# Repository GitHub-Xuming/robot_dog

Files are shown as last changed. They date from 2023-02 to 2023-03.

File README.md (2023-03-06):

# 开源四足机器狗
## 开源资料说明
* 硬件资料

Hardware/Model目录包含所有零件模型文件
* 软件资料

Software/Linux目录为上位机控制软件  
Software/STM32目录为单片机程序
## B站视频地址  
https://www.bilibili.com/video/BV1pX4y1D7ny/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
## 机械结构设计

    1.整机由12自由度四足机器狗以及一台6轴机械臂组成，四足机器人腿部采用了五连杆机构，之所以采用这样的结构，源于五连杆机构具有更大的承载  
    能力以及更好的刚性，但是也有它的缺点，运动范围相对串联腿小，不能做太大幅度动作，这个版本先使用并联腿，后面可以优化为串联结构！        
    2.五连杆两摆动臂采用浮动设计，中间加入减震弹簧，能减少对电机的冲击  
    3.腿部外伸自由度使用同步轮减速，减速比2.4，可以加大转矩以及减小电机间隙对输出的影响
    4.机身主要由两条碳纤维方管作为骨架支撑整个身体，其他运动部件以它为基准
    5.机械臂连杆使用碳纤维圆管连接
    6.机械臂末端安装机械爪，夹爪有弹簧缓冲结构  
## 关于舵机  

    1.机器狗使用12个mg958舵机，在对比多款舵机后，这个舵机是我认为性价比最高的，6.6V供电实测堵转扭矩能到18kg/cm,堵转电流5A，  
    响应速度也很OK,具体没测。6.6V供电电压由10个5A的降压模块而来，因舵机功率较大，所以受力较大的舵机都单独配一个降压模块，  
    这样一来整机的承载能力还是很可观的，具体可观看此视频：https://www.bilibili.com/video/BV1Lp4y1C75n/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
    2.机械臂电机使用总线舵机，某宝上买来的优必选舵机，10块钱左右一个，结合网友给出的研究资料（百度搜索白菜价舵机），成功驱动。  
    末端三个自由度使用的也是优必选的较小的一款，波特率1M，协议一致。整体来说，机械臂成本还是很低的
    
## 关于电路  
    开源资料未提供电路图，使用到的电路都非常简单  
    1.PWM舵机使用一组光耦隔离电路，总线舵机以及其他外设直接接单片机  
    2.FSR力传感器串联一个分压电阻直接接单片机  
    3.电源用继电器和二极管做了防反接保护，单片机和外设供电使用7805降压芯片  
 
## 关于板级通信
    控制器由BeagleBoneBlack开发板作为上位机，所有控制算法在上面完成，型号为STM32f407的单片机作为下位机，运行FreeRTOS操作系统
    负责外设数据采集和将上位机指令实时写到外设。  
    
    上位机与单片机通信使用的是全双工串口，以1M波特率运行，上位机实现了阻塞队列可多线程发起对单片机的传感器数据请求，单片机收到  
    请求后，立即采集数据并回复，同时上位机对当前数据进行计算，再下发控制数据到单片机... 整个过程看起开很繁琐，但是具有很高的实  
    时性，通过示波器观察，从上位机下发请求开始，到上位机再次下发完成控制数据，一共花费1.7ms
    
## 关于控制算法  
    重点说下鸡头模式原理，主要使用坐标系变换思想做到的，使用正向运动学以机器狗当前姿态为基础，将坐标系变换到机械臂坐标系，求逆矩阵，  
    再做逆向运动学，大概是这样的一个思路。  
    
    机械臂末端搭载了imu和光流传感器，都是用来测量末端的位移量，尝试了使用imu二次积分惯导解算位移，做闭环鸡头控制，无奈imu漂移太大，  
    整体效果较差，最终还是使用的了开环鸡头模式
    
    机器狗每条腿三个自由度，逆运动学使用代数法求解，可以得到三个角度，需要注意的是，有多组解，需要根据实际结构选择其中的一个，  
    机器狗扭身体动作原理同机械臂控制。

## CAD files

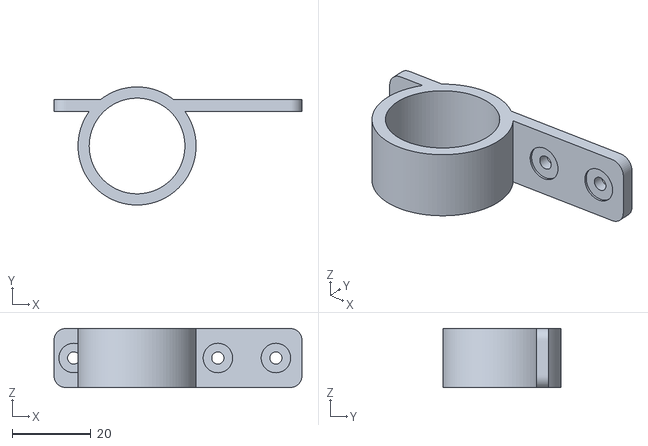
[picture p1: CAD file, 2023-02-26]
Hardtware/Model/同步轮支撑.stl
63.0 x 30.0 x 15.0

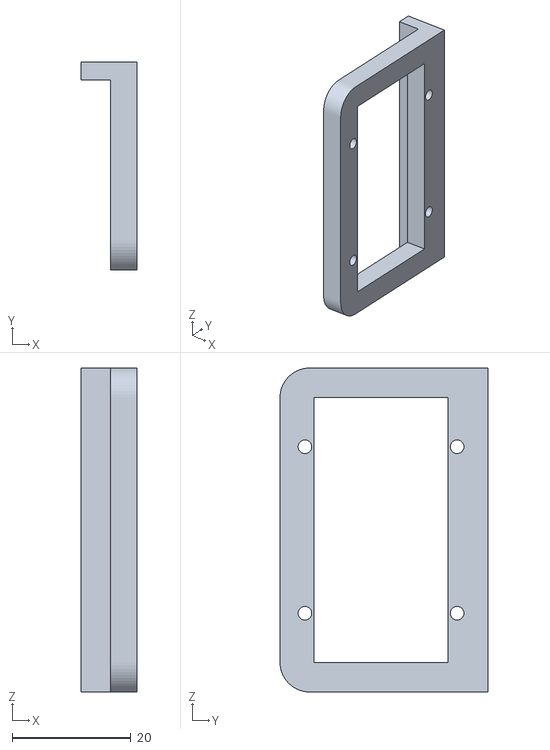
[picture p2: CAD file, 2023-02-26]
Hardtware/Model/机械臂旋转轴底座电机固定件2.stl
9.50 x 35.0 x 54.5

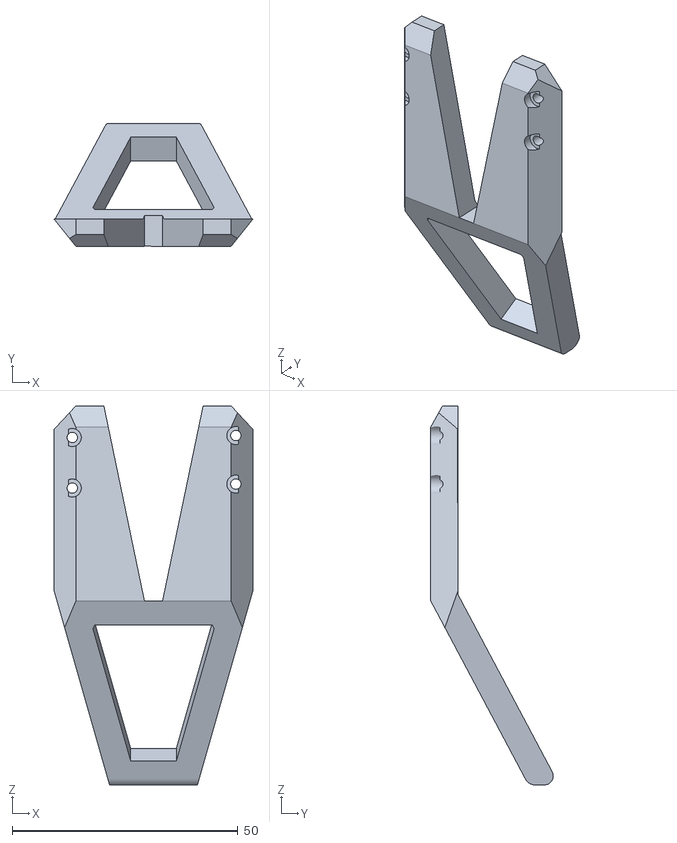
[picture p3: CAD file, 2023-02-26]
Hardtware/Model/机械爪上颌.stl
44.0 x 27.1 x 84.0

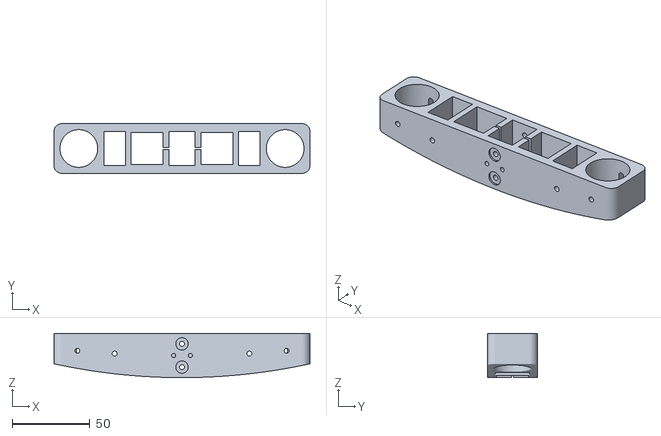
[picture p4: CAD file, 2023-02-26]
Hardtware/Model/机架1.stl
165.0 x 32.0 x 28.5

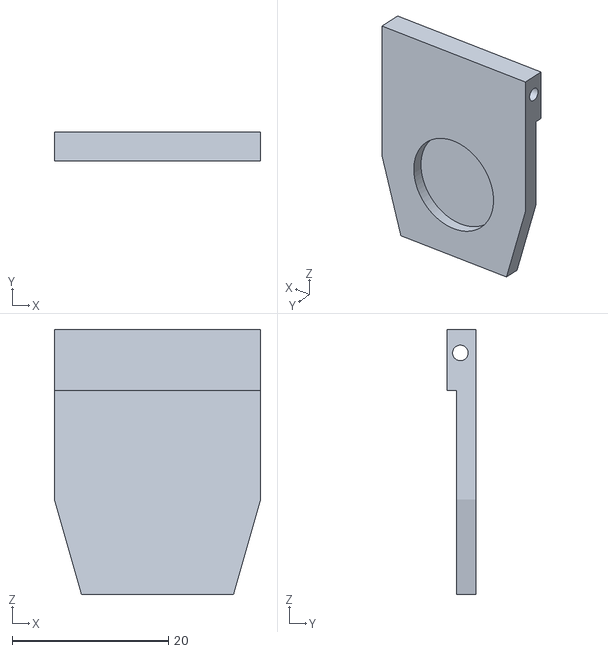
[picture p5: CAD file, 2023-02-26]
Hardtware/Model/机械爪FSR传感器座.stl
26.4 x 3.70 x 33.9

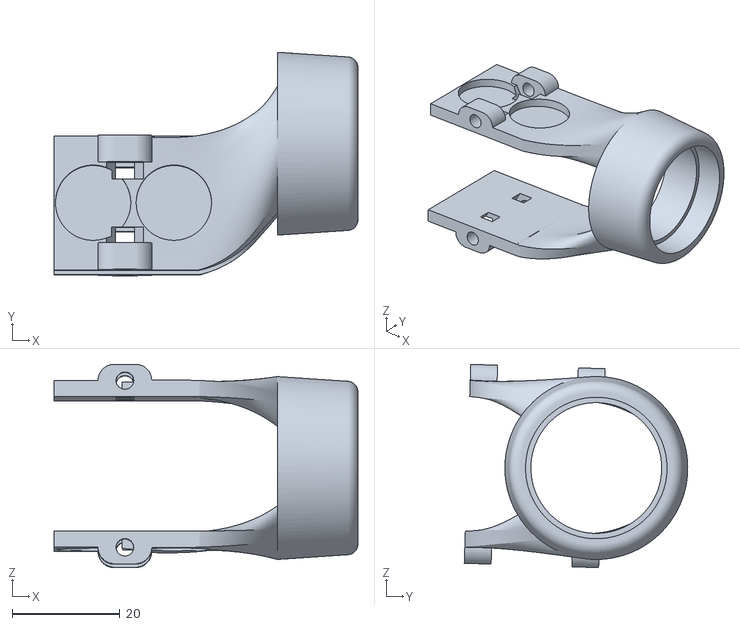
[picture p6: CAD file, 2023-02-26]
Hardtware/Model/腿部舵机输出支撑.stl
56.5 x 41.5 x 37.8

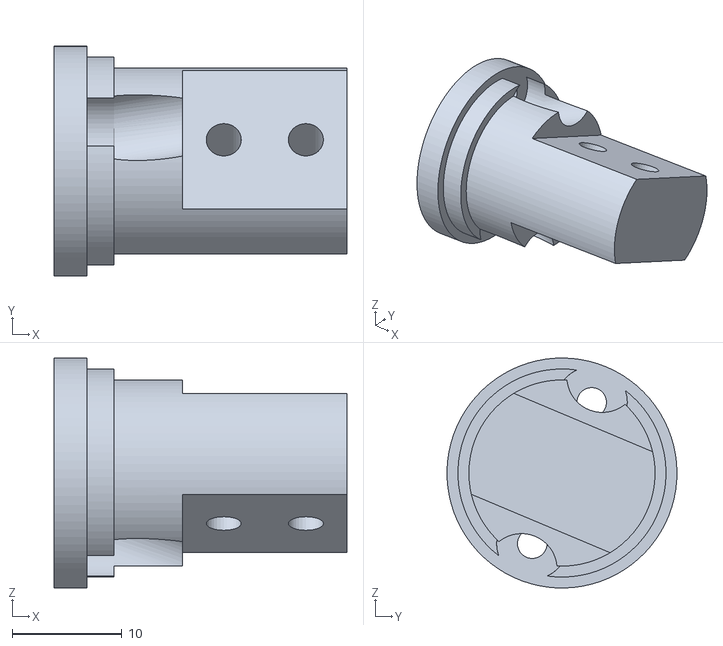
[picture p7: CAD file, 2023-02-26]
Hardtware/Model/腿部舵机法兰连接器.stl
26.8 x 21.0 x 21.0

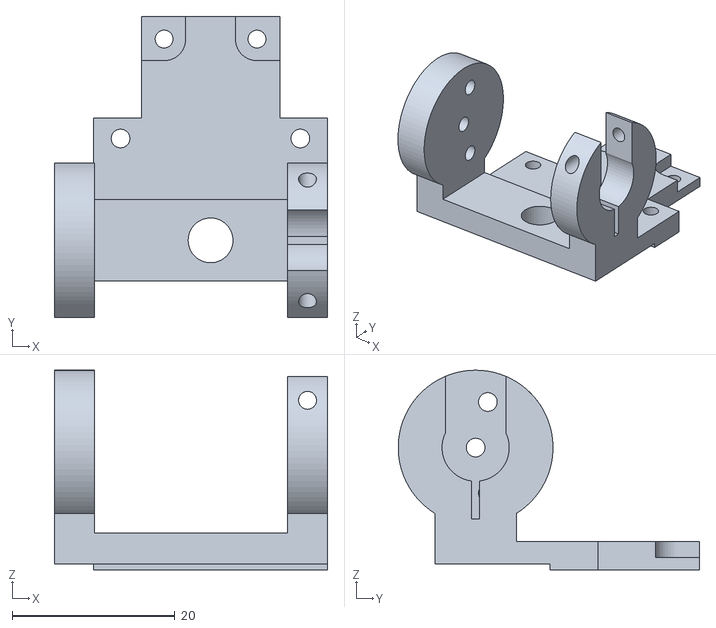
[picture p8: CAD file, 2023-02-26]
Hardtware/Model/机械臂五轴输出连接支架.stl
33.5 x 37.0 x 24.5

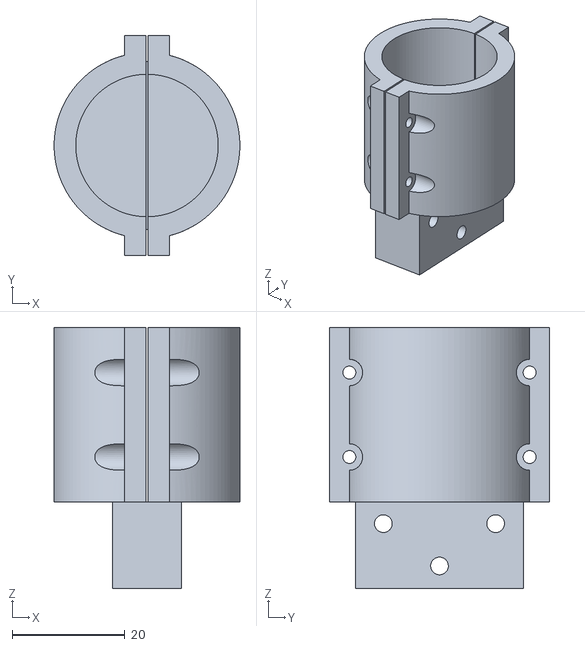
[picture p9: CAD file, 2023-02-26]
Hardtware/Model/机械臂二轴碳纤维连接件.stl
33.0 x 39.0 x 46.4

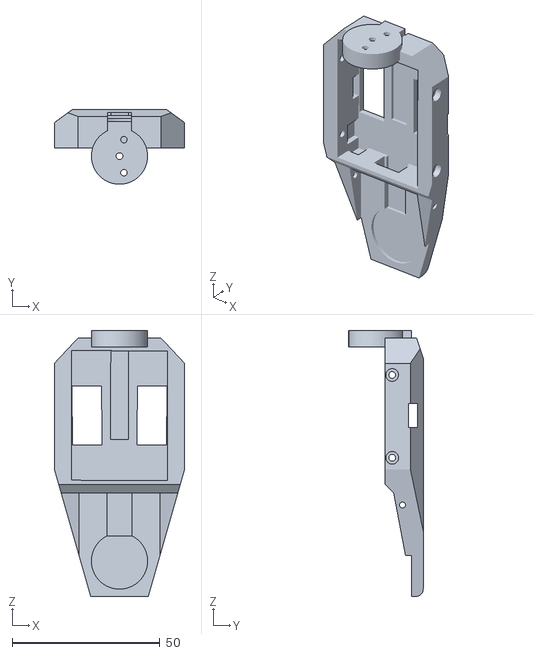
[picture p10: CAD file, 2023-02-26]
Hardtware/Model/机械爪底座.stl
44.0 x 25.2 x 89.9

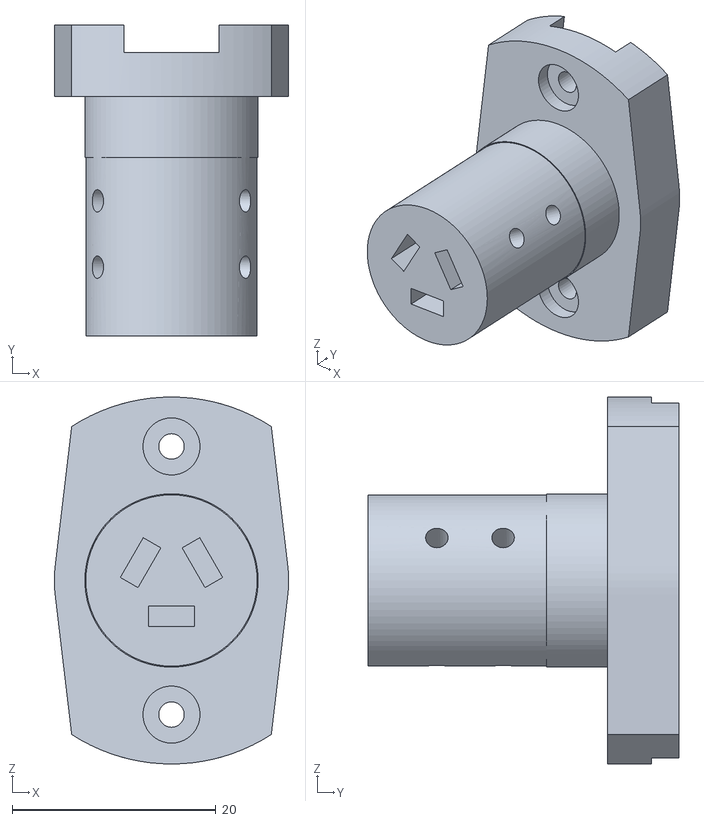
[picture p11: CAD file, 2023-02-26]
Hardtware/Model/机械臂底座电机输出轴.stl
23.0 x 30.5 x 36.0

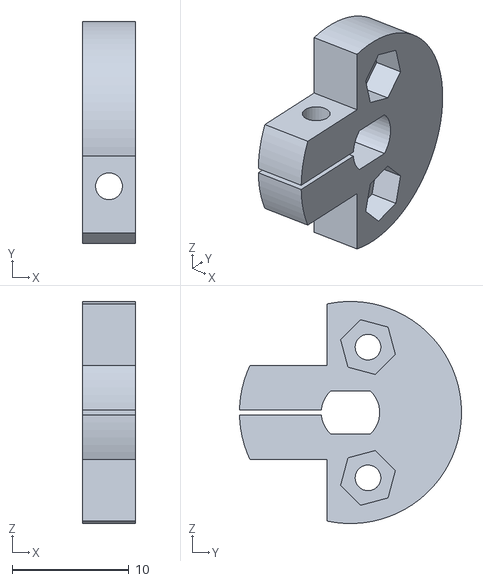
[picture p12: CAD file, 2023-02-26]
Hardtware/Model/机械臂五轴输出法兰盘.stl
4.50 x 19.0 x 19.0

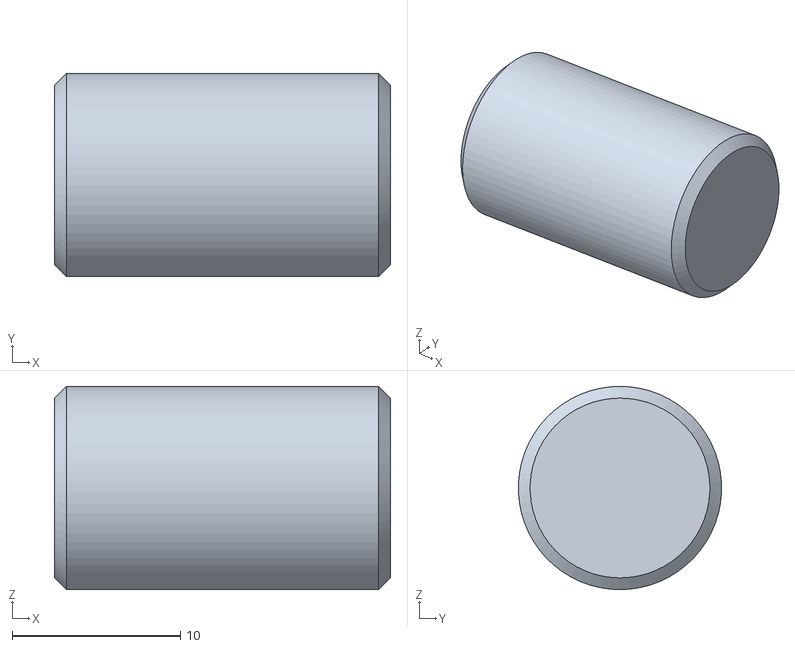
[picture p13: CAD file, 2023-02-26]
Hardtware/Model/腿部连杆轴.stl
20.0 x 12.1 x 12.1

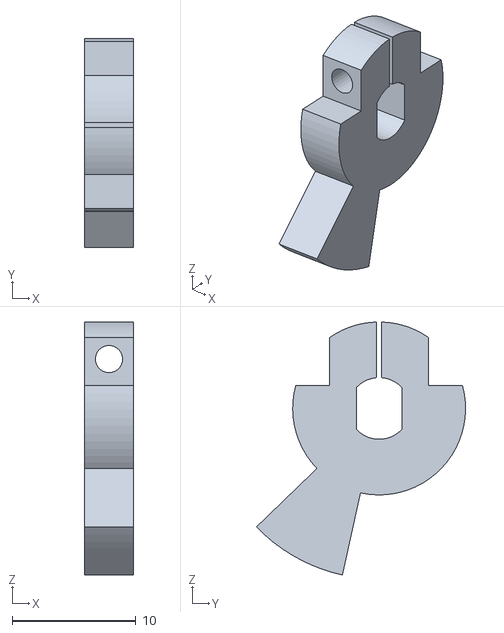
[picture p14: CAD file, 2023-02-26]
Hardtware/Model/机械爪电机输出轴法兰盘.stl
4.00 x 16.9 x 20.5

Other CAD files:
Hardtware/Model/机械臂四轴电机输出轴.stl
Hardtware/Model/机械爪电机输出轴.stl
Hardtware/Model/机械爪FSR传感器上盖.stl
Hardtware/Model/减震器弹簧座.stl
Hardtware/Model/减震器轴.stl
Hardtware/Model/同步轮减速电机座.stl
Hardtware/Model/同步轮大.stl
Hardtware/Model/同步轮小.stl
Hardtware/Model/同步轮边框大.stl
Hardtware/Model/同步轮连接器大.stl
Hardtware/Model/同步轮连接器小.stl
Hardtware/Model/机架2.stl
Hardtware/Model/机械爪上颌连接器1.stl
Hardtware/Model/机械爪上颌连接器2.stl
Hardtware/Model/机械爪减震机构2.stl
Hardtware/Model/机械臂三轴电机底座.stl
Hardtware/Model/机械臂三轴输出件1.stl
Hardtware/Model/机械臂三轴输出件2.stl
Hardtware/Model/机械臂二轴输出连接件.stl
Hardtware/Model/机械臂五轴碳纤维连接座.stl
Hardtware/Model/机械臂六轴电机固定支架.stl
Hardtware/Model/机械臂六轴输出法兰盘.stl
Hardtware/Model/机械臂四轴电机支架.stl
Hardtware/Model/机械臂四轴电机输出法兰盘.stl
Hardtware/Model/机械臂四轴输出支架.stl
Hardtware/Model/机械臂四轴输出碳纤维连接座.stl
Hardtware/Model/机械臂底座电机连接件1.stl
Hardtware/Model/机械臂底座电机连接件2.stl
Hardtware/Model/机械臂旋转轴底座.stl
Hardtware/Model/机械臂旋转轴底座电机固定件1.stl
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

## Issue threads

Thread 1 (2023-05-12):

The meaning of bodyPeakPoint

1874ruanshaodong, 2023-05-12:
Hi, what does bodyPeakPoint mean? Is it meaning that is the four vertices of the torso? Thanks.

GitHub-Xuming, 2023-05-13:
Yes, that’s correct. If we regard the four legs as four mechanical arms, then “bodyPeakPoint” is the origin position of each mechanical arm.

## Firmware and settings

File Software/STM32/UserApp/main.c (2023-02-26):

#include "robot_dog.h"
#include "robot_arm.h"
#include "timer.h"
#include "remote_ctrl.h"
#include "FreeRTOS.h"
#include "task.h"
#include "SEGGER_RTT.h"

int main()
{
	NVIC_PriorityGroupConfig(NVIC_PriorityGroup_4);	
	delay_init(168);
	SysTimerInit(1000 - 1, 84 - 1);
	SeggerInit();

	RemoteCtrlInit();
	ComHostInit();
	RobotArmInit();
	RobotDogInit();

	vTaskStartScheduler();
}

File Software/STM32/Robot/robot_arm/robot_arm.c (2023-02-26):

#include "robot_arm.h"
#include "math.h"
#include "usart3.h"
#include "uart4.h"
#include "delay.h"
#include "SEGGER_RTT.h"
#include "com_host.h"
#include "remote_ctrl.h"
#include "inertial_nav.h"
#include "FreeRTOS.h"
#include "task.h"
#include "semphr.h"

#define 	RobotArmCTRL_TASK_PRIO 			2  
#define 	RobotArmCTRL_STK_SIZE 			128 
#define 	ARM_ANGLE_ASK_TASK_PRIO 		2  
#define 	ARM_ANGLE_ASK_STK_SIZE 			128 
#define     ARM_CTRL_BAUD_RATE      		1000000 
#define     IMU_COM_BAUD_RATE      			921600 

TaskHandle_t Arm_Angle_Ask_Task_Handler; 
TaskHandle_t RobotArmCtrlTask_Handler;
void RobotArmAngleAskTask(void *p_arg); 
void RobotArmCtrlTask(void *p_arg); 
void RobotArmGPIO_Init();

uint8_t g_send_buff[10] = {FRAME_HEAD_1, FRAME_HEAD_2, 0x04, 0xD4, 0x00, 0x00, 0x00, 0x00};
uint8_t g_servo_kind = 0;
uint8_t g_id_convert_tb[7] = {1, 21, 3, 4, 5, 6, 7};

ACK_FRAM g_arm_res;
ServoInfo g_servo_info[7] = { 0 };
ArmAngle *g_arm_angle = NULL;
xSemaphoreHandle g_xArmAngleResSemaphore;
xSemaphoreHandle g_xRobotArmCtrlSemaphore;

/**
  * @brief  
  * @param  
  * @param 
  */
void RobotArmInit()
{
	Adc_Init();
	RobotArmGPIO_Init();
	Uart4Init(ARM_CTRL_BAUD_RATE); //机械臂
	//USART5_Init(IMU_COM_BAUD_RATE); //imu
	TIM1_CH1_Cap_Init(0xFFFF, 840 - 1); //光流传感器
	NavigationInit();
	/*servo 零点偏置初始化 原则：将舵机位置摆放到机械臂坐标系零点位置后，读取的角度值即为:offset*/
	g_servo_info[0].offset = 0;
	g_servo_info[1].offset = 0;
	g_servo_info[2].offset = 0;
	g_servo_info[3].offset = 0;
	g_servo_info[4].offset = 0;
	g_servo_info[5].offset = 120;
	g_servo_info[6].offset = 0;

	/*舵机id赋值，位置和读取标志清零*/
	for(int i = 0; i < 7; i++)
	{
		g_servo_info[i].id = g_id_convert_tb[i];
		g_servo_info[i].pos = 0;
		g_servo_info[i].read_flg = 0;
	}
	xTaskCreate((TaskFunction_t )RobotArmAngleAskTask,
		(const char* )"RobotArmAngleAskTask",
		(uint16_t )ARM_ANGLE_ASK_STK_SIZE,
		(void* )NULL,
		(UBaseType_t )ARM_ANGLE_ASK_TASK_PRIO,
		(TaskHandle_t* )&Arm_Angle_Ask_Task_Handler);

	xTaskCreate((TaskFunction_t )RobotArmCtrlTask,
		(const char* )"RobotArmCtrlTask",
		(uint16_t )RobotArmCTRL_STK_SIZE,
		(void* )NULL,
		(UBaseType_t )RobotArmCTRL_TASK_PRIO,
		(TaskHandle_t* )&RobotArmCtrlTask_Handler);
}

/**
  * @brief  
  * @param  
  * @param 
  */
void RobotArmGPIO_Init()
{ 
	GPIO_InitTypeDef  GPIO_InitStructure;
	RCC_AHB1PeriphClockCmd(RCC_AHB1Periph_GPIOD, ENABLE);

	GPIO_InitStructure.GPIO_Pin = GPIO_Pin_0 | GPIO_Pin_1;
	GPIO_InitStructure.GPIO_Mode = GPIO_Mode_OUT;
	GPIO_InitStructure.GPIO_OType = GPIO_OType_PP;
	GPIO_InitStructure.GPIO_Speed = GPIO_Speed_100MHz;
	GPIO_InitStructure.GPIO_PuPd = GPIO_PuPd_UP;
	GPIO_Init(GPIOD, &GPIO_InitStructure);

	GPIO_SetBits(GPIOD,GPIO_Pin_0 | GPIO_Pin_1);
	/*Arm角度请求信号量创建*/
	vSemaphoreCreateBinary(g_xArmAngleResSemaphore);
	if(g_xArmAngleResSemaphore != NULL)
	{
		xSemaphoreTake(g_xArmAngleResSemaphore, 0);
	}
	else
	{
		for(;;){}
	}
	/*Arm控制信号量创建*/
	vSemaphoreCreateBinary(g_xRobotArmCtrlSemaphore);
	if(g_xRobotArmCtrlSemaphore != NULL)
	{
		xSemaphoreTake(g_xRobotArmCtrlSemaphore, 0);
	}
	else
	{
		for(;;){}
	}
}

/**
  * @brief  
  * @param  
  * @param 
  */
void RobotArmAngleSemaphoreGive()
{
	portBASE_TYPE xHigherPriorityTaskWoken;
	xSemaphoreGiveFromISR(g_xArmAngleResSemaphore, &xHigherPriorityTaskWoken);
	if(xHigherPriorityTaskWoken)
	{
		portYIELD_FROM_ISR(xHigherPriorityTaskWoken);
	}
}

/**
  * @brief  
  * @param  
  * @param 
  */
void RobotArmCtrlSemaphoreGive()
{
	portBASE_TYPE xHigherPriorityTaskWoken;
	xSemaphoreGiveFromISR(g_xRobotArmCtrlSemaphore, &xHigherPriorityTaskWoken);
	if(xHigherPriorityTaskWoken)
	{
		portYIELD_FROM_ISR(xHigherPriorityTaskWoken);
	}
}

/**
  * @brief  
  * @param  
  * @param 
  */
void RobotArmAngleRes()
{
	g_arm_res.head = UART_DATA_HEAD;
	g_arm_res.function_code = TYPE_ARM_POS_RES; 
	g_arm_res.data_len = 14; 
	uint16_t tmp = 0;
	for(int i = 0; i < 7; i++)
	{
		tmp = g_servo_info[i].pos * ANGLE_CONVERT_RATE;
		g_arm_res.data[i * 2] = ((tmp >> 8) & 0x00ff);
		g_arm_res.data[i * 2 + 1] = (tmp & 0x00ff);
	}
	ComHostPacketToQueue(&g_arm_res, 0);
}

/**
  * @brief  
  * @param  
  * @param 
  */
void RobotArmAngleAskTask(void *p_arg)
{
	int flag_sum = 0;
	while(1)
	{
		if(xSemaphoreTake(g_xArmAngleResSemaphore, 100000) == pdTRUE)
		{
			USART_Cmd(UART4, ENABLE); 
			while(1)
			{
				RobotArmServoStartPosRead();  //正常情况下，发送函数执行完成，已经收到舵机回复了
				for(int i = 0; i < 7; i++)
				{
					flag_sum += g_servo_info[i].read_flg;
				}
				if(7 == flag_sum)
				{
					break;
				}
				flag_sum = 0;
				vTaskDelay(20);
			}
			USART_Cmd(UART4, DISABLE);  
			for(int i = 0; i < 7; i++)
			{
				g_servo_info[i].read_flg = 0;
			}
			RobotArmAngleRes();
		}
	}
}

/**
  * @brief  
  * @param  
  * @param 
  */
void RobotArmAngleCtrlValue(ArmAngle *angle)
{
	g_arm_angle = angle;
}

/**
  * @brief  
  * @param  
  * @param 
  */
void RobotArmCtrlTask(void *pvParameters)
{
	float delta_angle = 0.0;
	while(1)
	{
		if(xSemaphoreTake(g_xRobotArmCtrlSemaphore, 100000) == pdTRUE)
		{
			//send angle to servo
			RobotArmAllServoPosCtrl();
		}
	}
}

/**
  * @brief  
  * @param  
  * @param 
  */
void RobotArmAllServoPosCtrl()
{
	int ctrl_angle = 0;
	float delta_angle = 0.0;

	Uart4Init(115200);
	g_servo_kind = SERVO_BIG;
	for(int i = 0; i < 3; i++)
	{
		ctrl_angle = RobotArmServoAngleOptimizing(g_arm_angle->axis_angle[i]);
		delta_angle = ctrl_angle - g_servo_info[i].last_ctrl_angle; //突变计算
		if(ABS(delta_angle) < ARM_CTRL_SAFE_ANGLE)  //位置突变保护
		{
			if(i == 1)
			{
				RobotArmServoPosCtrl(22, RobotArmAxis2AngleConvert(ctrl_angle), 0, 0);
				vTaskDelay(2);  //必要延时，舵机回复数据较慢
			}
			RobotArmServoPosCtrl(g_id_convert_tb[i], ctrl_angle, 0, 0);
			vTaskDelay(2);
			g_servo_info[i].last_ctrl_angle = ctrl_angle;
		}
	}

	Uart4Init(1000000);
	g_servo_kind = SERVO_SMALL;
	for(int i = 3; i < 7; i++)
	{
		/*对控制的float角度进行优化处理*/
		ctrl_angle = RobotArmServoAngleOptimizing(g_arm_angle->axis_angle[i]);
		delta_angle = ctrl_angle - g_servo_info[i].last_ctrl_angle; //突变计算
		if(ABS(delta_angle) < ARM_CTRL_SAFE_ANGLE)  //位置突变保护
		{
			RobotArmServoPosCtrl(g_id_convert_tb[i], ctrl_angle, 0, 0);
			vTaskDelay(1);
			g_servo_info[i].last_ctrl_angle = ctrl_angle;
		}
	}
}

// float ConvertServo2Arm(ServoInfo *servo, float angle)
// {
// 	float out = 0;
// 	out = angle - servo->offset;
// 	return out < 0 ? (out + 360) : out;
// }

// float ConvertArm2Servo(ServoInfo *servo, float angle)
// {
// 	float out = 0;
// 	out = angle + servo->offset;
// 	return out > 360 ? (out - 360) : out;
// }

/**
  * @brief  
  * @param  
  * @param 
  */
void RobotArmCkeckAndSend()
{
	uint8_t check_sum = 0;

	for(int i = 2; i < 8; i++)
	{
		check_sum += g_send_buff[i];
	}
	g_send_buff[8] = check_sum;
	g_send_buff[9] = FRAME_TAIL;
	
	EN_T = 0;
	EN_R = 1;
	for(int i = 0; i < 10; i++)
	{
		Uart4SendByte(g_send_buff[i]);
	}
	if(g_servo_kind == SERVO_SMALL)
	{
		delay_us(30);  //min 6us
	}
	if(g_servo_kind == SERVO_BIG)
	{
		delay_us(70);  //min 6us
	}
	EN_T = 1;
	EN_R = 0;
}
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

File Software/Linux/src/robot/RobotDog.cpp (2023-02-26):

#include "RobotDog.h"
#include <math.h>
#include "my_debug.h"
#include "DataProgress.h"

using namespace std;

RobotDog::RobotDog()
{
	m_send_queue_ = std::make_shared<BlockQueue<std::vector<char>>>(10);

	/*leg编号初始化*/
	robot.legFR.leg_number = leg_1;
	robot.legBR.leg_number = leg_2;
	robot.legBL.leg_number = leg_3;
	robot.legFL.leg_number = leg_4;

	/*机器人body_move初始化*/
	robot.body.move_x = 0;
	robot.body.move_y = 0;
	robot.body.move_z = 0;

	/*机器人坐标系原点初始化*/
	robot.body.bodyCoorZeroPoint.x = 0;  
	robot.body.bodyCoorZeroPoint.y = 0;
	robot.body.bodyCoorZeroPoint.z = 0;

	/*机器人中心点偏移量初始化*/
	robot.body.body_centre_move_x = 0;
	robot.body.body_centre_move_y = 0;
	robot.body.body_centre_move_z = 0;

	/*四条腿顶点偏移*/
	robot.legFR.bodyPeakPoint.x = -(DOG_BODY_LENGTH/2.0 - robot.body.body_centre_move_x);
	robot.legFR.bodyPeakPoint.y = DOG_BODY_WIDE/2.0 - robot.body.body_centre_move_y;
	robot.legFR.bodyPeakPoint.z = 0;

	robot.legBR.bodyPeakPoint.x = DOG_BODY_LENGTH/2.0 + robot.body.body_centre_move_x;
	robot.legBR.bodyPeakPoint.y = DOG_BODY_WIDE/2.0 - robot.body.body_centre_move_y;
	robot.legBR.bodyPeakPoint.z = 0;

	robot.legBL.bodyPeakPoint.x = DOG_BODY_LENGTH/2.0 + robot.body.body_centre_move_x;
	robot.legBL.bodyPeakPoint.y = -(DOG_BODY_WIDE/2.0 + robot.body.body_centre_move_y);
	robot.legBL.bodyPeakPoint.z = 0;

	robot.legFL.bodyPeakPoint.x = -(DOG_BODY_LENGTH/2.0 - robot.body.body_centre_move_x);
	robot.legFL.bodyPeakPoint.y = -(DOG_BODY_WIDE/2.0 + robot.body.body_centre_move_y);
	robot.legFL.bodyPeakPoint.z = 0;

	m_send_data_.resize(24);
	m_thread_run_ = true;
	RobotDogRun();
}

RobotDog::~RobotDog()
{
	m_thread_run_ = false;
}

void RobotDog::RobotDogPoseFeedback(Pose &pose)
{
	m_robot_pose_.x = robot.body.moveVal.move_axis_x;
	m_robot_pose_.y = robot.body.moveVal.move_axis_y;
	m_robot_pose_.z = robot.body.moveVal.move_axis_z;
	m_robot_pose_.roll = robot.body.rotateVal.rot_axis_x;
	m_robot_pose_.pitch = robot.body.rotateVal.rot_axis_y;
	m_robot_pose_.yaw = robot.body.rotateVal.rot_axis_z;
	pose = m_robot_pose_;
}

void RobotDog::RobotDogCtrl(Pose posture, FootCoord foot_pos, std::vector<uint8_t> &out)
{
	robot.body.moveVal.move_axis_x = posture.x;
	robot.body.moveVal.move_axis_y = posture.y;
	robot.body.moveVal.move_axis_z = posture.z;
	robot.body.rotateVal.rot_axis_x = posture.roll;
	robot.body.rotateVal.rot_axis_y = posture.pitch;
	robot.body.rotateVal.rot_axis_z = posture.yaw;

	robot.legFR.world_coor_point.x = foot_pos.foot_FR.x;
	robot.legFR.world_coor_point.y = foot_pos.foot_FR.y;
	robot.legFR.world_coor_point.z = foot_pos.foot_FR.z;

	robot.legBR.world_coor_point.x = foot_pos.foot_BR.x;
	robot.legBR.world_coor_point.y = foot_pos.foot_BR.y;
	robot.legBR.world_coor_point.z = foot_pos.foot_BR.z;

	robot.legBL.world_coor_point.x = foot_pos.foot_BL.x;
	robot.legBL.world_coor_point.y = foot_pos.foot_BL.y;
	robot.legBL.world_coor_point.z = foot_pos.foot_BL.z;

	robot.legFL.world_coor_point.x = foot_pos.foot_FL.x;
	robot.legFL.world_coor_point.y = foot_pos.foot_FL.y;
	robot.legFL.world_coor_point.z = foot_pos.foot_FL.z;

	RobotDogProcessFlow();
	/*pos and en ctrl*/
	ServoAngleConstruct();
	out = m_send_data_;
}

void RobotDog::EN_Ctrl(bool en)
{
	RobotDogServoEnCtrl(en);
}

void RobotDog::RobotDogServoEnCtrl(bool ctrl)
{
	m_robot_enable_ = ctrl;
}

void RobotDog::RobotDogProcessFlow()
{
	/*控制body姿态，三个平移和旋转*/
	RobotDogRotMove(robot.body.rotateVal,robot.body.moveVal);

	/*正向运动学到各个关节，将世界坐标系描述的点转换到局部坐标系描述*/ 
	RobotDogInvForward(&robot.legFR);
	RobotDogInvForward(&robot.legBR);
	RobotDogInvForward(&robot.legBL);
	RobotDogInvForward(&robot.legFL);

	/*逆解，得到原始角度值*/
	LegInverseResolving(&robot.legFR);
	LegInverseResolving(&robot.legBR);
	LegInverseResolving(&robot.legBL);
	LegInverseResolving(&robot.legFL);

	/*得到五连杆机构的值*/
	GetFiveLinkAngle(&robot.legFR);
	GetFiveLinkAngle(&robot.legBR);
	GetFiveLinkAngle(&robot.legBL);
	GetFiveLinkAngle(&robot.legFL);

	/*转换到电机的角度值*/
	GetFiveLinkToMotor(&robot.legFR);
	GetFiveLinkToMotor(&robot.legBR);
	GetFiveLinkToMotor(&robot.legBL);
	GetFiveLinkToMotor(&robot.legFL);
}

void RobotDog::RobotDogRun()
{
    m_robot_thread_ = std::thread([this]
    {
        while(m_thread_run_) 
		{
			//TODO:
			std::this_thread::sleep_for(std::chrono::milliseconds(1000));    
		}
    });
}

void RobotDog::RobotDogRotMove(BodyRot rotateVal,BodyMove moveVal)
{
	float move_body[4][4] = { { 1,0,0,0 },{ 0,1,0,0 },{ 0,0,1,0 },{ 0,0,0,1 } };
	float ret_body_x[4][4] = { { 1,0,0,0 },{ 0,1,0,0 },{ 0,0,1,0 },{ 0,0,0,1 } };
	float ret_body_y[4][4] = { { 1,0,0,0 },{ 0,1,0,0 },{ 0,0,1,0 },{ 0,0,0,1 } };
	float ret_body_z[4][4] = { { 1,0,0,0 },{ 0,1,0,0 },{ 0,0,1,0 },{ 0,0,0,1 } };
	float mid_matrix_1[4][4] = { { 1,0,0,0 },{ 0,1,0,0 },{ 0,0,1,0 },{ 0,0,0,1 } };
	float mid_matrix_2[4][4] = { { 1,0,0,0 },{ 0,1,0,0 },{ 0,0,1,0 },{ 0,0,0,1 } };

	/*矩阵初始化*/
	move_body[0][3] = moveVal.move_axis_x;
	move_body[1][3] = moveVal.move_axis_y;
	move_body[2][3] = moveVal.move_axis_z;
	
	ret_body_x[1][1] = cos(rotateVal.rot_axis_x);
	ret_body_x[1][2] = -sin(rotateVal.rot_axis_x);
	ret_body_x[2][1] = sin(rotateVal.rot_axis_x);
	ret_body_x[2][2] = cos(rotateVal.rot_axis_x);
	
	ret_body_y[0][0] = cos(rotateVal.rot_axis_y);
	ret_body_y[0][2] = sin(rotateVal.rot_axis_y);
	ret_body_y[2][0] = -sin(rotateVal.rot_axis_y);
	ret_body_y[2][2] = cos(rotateVal.rot_axis_y);	
	
	ret_body_z[0][0] = cos(rotateVal.rot_axis_z);
	ret_body_z[0][1] = -sin(rotateVal.rot_axis_z);
	ret_body_z[1][0] = sin(rotateVal.rot_axis_z);
	ret_body_z[1][1] = cos(rotateVal.rot_axis_z);	
	
	MatrixCalc::MatrixMull(move_body,ret_body_x,mid_matrix_1);    
	MatrixCalc::MatrixMull(mid_matrix_1,ret_body_y,mid_matrix_2);	 
	MatrixCalc::MatrixMull(mid_matrix_2,ret_body_z,mid_matrix_1);  
	MatrixCalc::MatrixTransmit(mid_matrix_1,robot.body.postureMatrix); 
}

void RobotDog::RobotDogInvForward(Leg *leg)
{
	float rot_y[4][4] = { { 1,0,0,0 },{ 0,1,0,0 },{ 0,0,1,0 },{ 0,0,0,1 } };
	float body_point[4][4] = { { 1,0,0,0 },{ 0,1,0,0 },{ 0,0,1,0 },{ 0,0,0,1 } };
	float mid_matrix_1[4][4] = { { 1,0,0,0 },{ 0,1,0,0 },{ 0,0,1,0 },{ 0,0,0,1 } };
	float mid_matrix_2[4][4] = { { 1,0,0,0 },{ 0,1,0,0 },{ 0,0,1,0 },{ 0,0,0,1 } };
	float mid_matrix_inv[3] = { 0 }; 

	rot_y[0][0] = cos(ROT_Y);
	rot_y[0][2] = sin(ROT_Y);
	rot_y[2][0] = -sin(ROT_Y);
	rot_y[2][2] = cos(ROT_Y);

	body_point[0][3] = leg->bodyPeakPoint.x;
	body_point[1][3] = leg->bodyPeakPoint.y;

	MatrixCalc::MatrixMull(robot.body.postureMatrix, body_point, mid_matrix_1);
	MatrixCalc::MatrixMull(mid_matrix_1, rot_y, mid_matrix_2);	
	MatrixCalc::MatrixInv(mid_matrix_2, mid_matrix_1);	
	for (uint8_t i = 0; i < 3; i++)  	//将求逆后矩阵乘世界坐标系中给定的点，得到点在每条腿坐标系中的描述 
	{ 
		mid_matrix_inv[i] = mid_matrix_1[i][0] * leg->world_coor_point.x + mid_matrix_1[i][1] * leg->world_coor_point.y + mid_matrix_1[i][2] * leg->world_coor_point.z + mid_matrix_1[i][3] * 1.0;
	}	
	leg->local_coor_point.x = mid_matrix_inv[0];
	leg->local_coor_point.y = mid_matrix_inv[1];
	leg->local_coor_point.z = mid_matrix_inv[2];
}
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
